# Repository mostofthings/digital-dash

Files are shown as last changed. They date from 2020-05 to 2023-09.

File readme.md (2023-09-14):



# Raspberry Pi Digital Dash

The goal of this project is to create a universal digital gauge readout for racecar applications. The core aims of this project are:

## To display easy to read data in an attractive format.

The final product should, as much as possible, look as good or better than a bank of physical gauges.



## To offer short-term historical data readout.

When driving a racecar under duress, it's often impossible to look at 7-plus-gauges and make sure that everything seems in spec. The ultimate goal of this project is to add a chart of recent historical data - think like a CPU monitor - of relevant data over a short period of time. In the pits or on the grid, the driver can peek at the data and make sure that all the systems of the car are healthy and well, even when operating under extreme conditions.

## To provide this functionality at minimal cost

Fully outfitting a racecar dash can easily cost a couple thousand bucks. One of the goals of this project is to minimize financial input and maximize efficacy and accuracy. That, friends, is the American Dream. To this end, the physical hardware involved is as inexpensive as possible, and the sensors used will, as much as possible, be all off-the-shelf, readily-available, universally-fittable ones from your favorite Large Corporate Autoparts Store.

On the computer hardware side, this project utilizes an Arduino Uno, a Raspberry Pi, and corresponding Pi 7" touch screen. I will be making use of a 3D printer, and wherever possible will be providing .stl files of any custom parts made. 

## To calibrate those sensors as accurately as possible

It's one thing for it to be cheap, and another for it to be cheap AND good. Most automotive sensors operate by providing various levels of resistance under different circumstance, and using the Arduino, we use that resistance to monitor a reference voltage. Most sensors - cheap or expensive, are assumed to have a linear response. Early testing for this project indicates that that's not always the case. 

While Mostly linear, a more curvilinear response is often seen. While this may not seem like that big of a deal, that's wholly dependent on where those curves are. In testing for the water temp sensor, the response of the sensor changes almost exponentially at the top end of its operating range - exactly where we need it the most. Various strategies will be employed to make sure that the readings on the gauge are the actual conditions going on in the car. 

## To allow this project to be replicated by others

If you too have around $250, know your way around a Raspberry Pi functionally well, and possess a willingness to walk into an Autozone, you too can replicate this exact setup. I have in MY mind specific goals for functionality, but I'm sure others may want different results to match with their particular corner of the vehicular world. Other projects similar to this one already exist, but hopefully by providing expanded functionality and ample information, this too can gain a bit of traction. Ultimately, I'll be happy to have the results of this project for myself, but I'd love it if anyone else out there found some utility out of it as well.

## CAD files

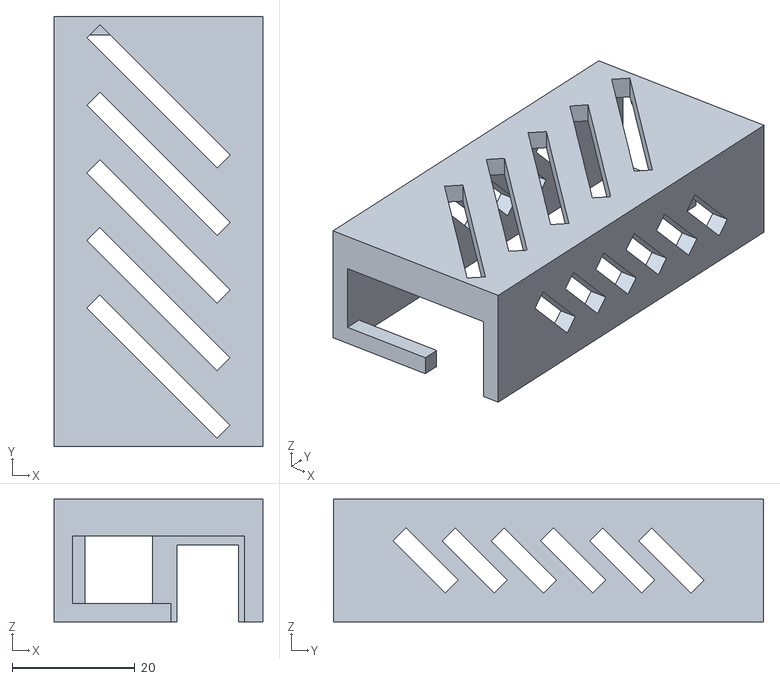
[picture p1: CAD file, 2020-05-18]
3d-print-stl-files/buck-converter-case-top.stl
34.0 x 70.0 x 20.0

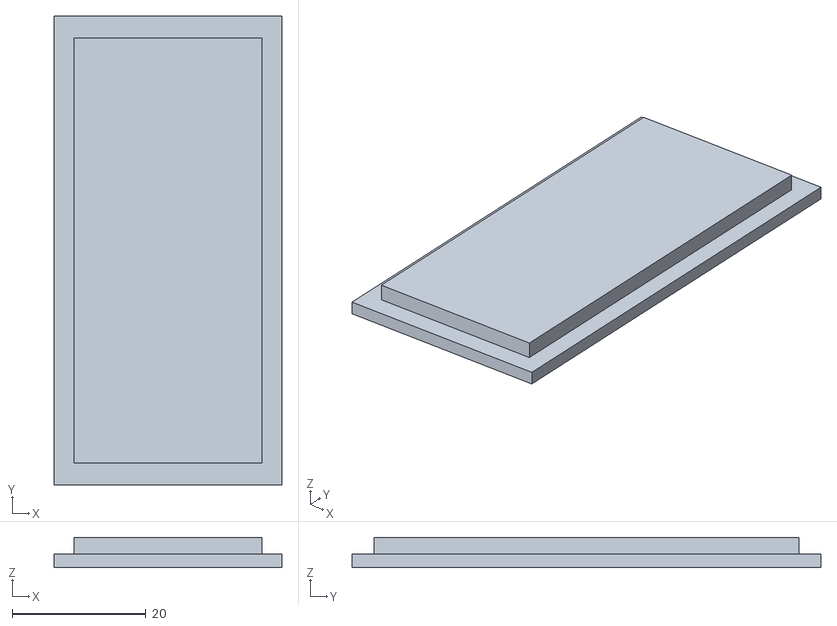
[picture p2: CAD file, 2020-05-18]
3d-print-stl-files/buck-converter-case-bottom.stl
34.0 x 70.0 x 4.50

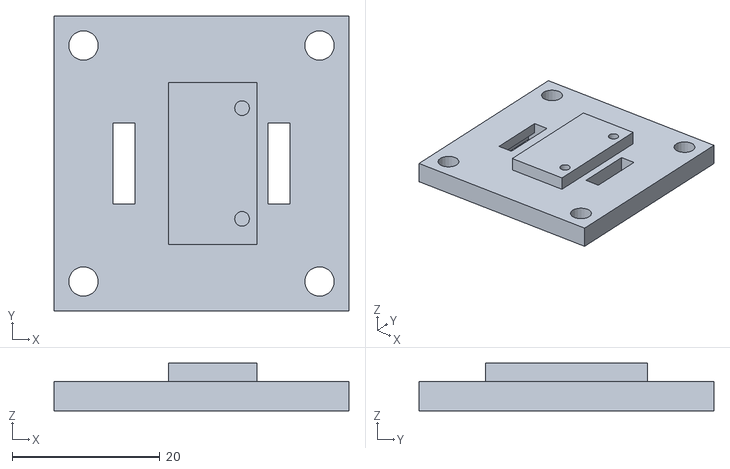
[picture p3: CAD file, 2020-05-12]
3d-print-stl-files/MMA8451 static car mount base.stl
40.0 x 40.0 x 6.50

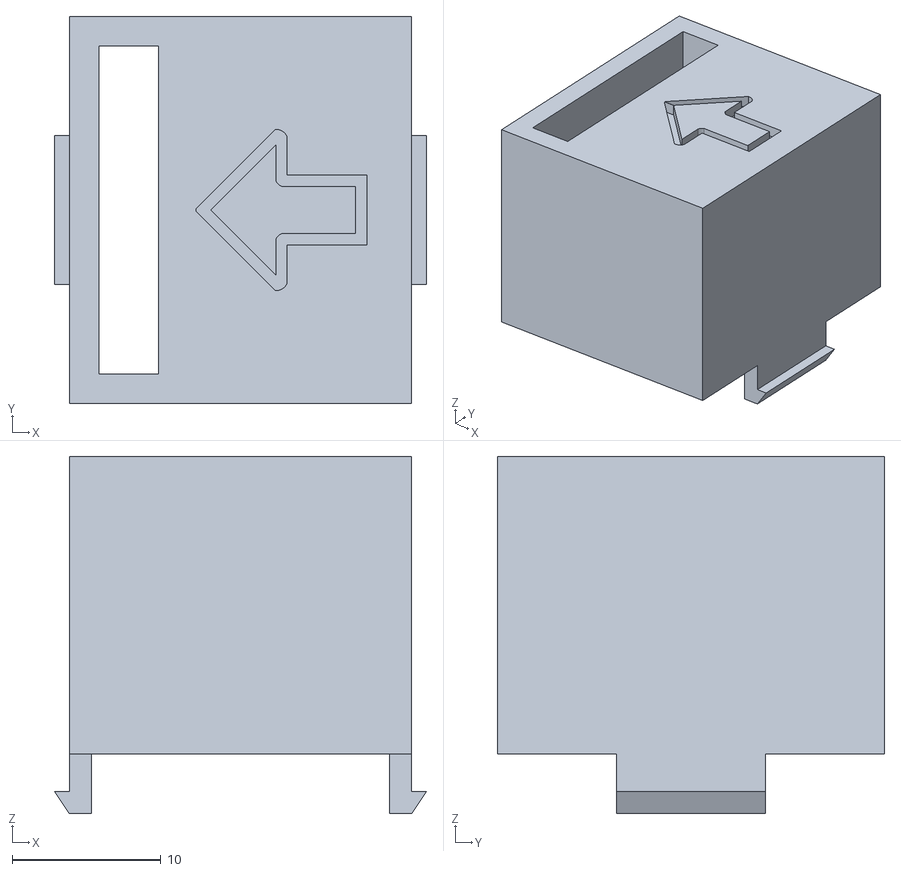
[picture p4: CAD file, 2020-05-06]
3d-print-stl-files/MMA8451 static car mount top.stl
25.0 x 26.0 x 24.0

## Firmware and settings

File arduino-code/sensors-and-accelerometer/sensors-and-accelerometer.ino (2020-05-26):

#include <math.h>
#include <Wire.h>
#include <Adafruit_MMA8451.h>
#include <Adafruit_Sensor.h>
#include <Adafruit_NeoPixel.h>
#ifdef __AVR__
#include <avr/power.h> // Required for 16 MHz Adafruit Trinket
#endif

#define PIXEL_PIN    6  // Digital IO pin connected to the NeoPixels.
#define PIXEL_COUNT 16  // Number of NeoPixels

Adafruit_NeoPixel strip(PIXEL_COUNT, PIXEL_PIN, NEO_GRB + NEO_KHZ800);

Adafruit_MMA8451 mma = Adafruit_MMA8451();

char receivedChar;
String receivedMessage;

int rawValue;
unsigned long duration;
float periodInSeconds;
float unroundedRPM;
int roundedRPM;
int rpmToSend;
int lastKnownGoodRPM;
int blinkCounter = 0;
unsigned long timeNow;
bool isDemo = false;
unsigned long demoStart;
int demoDelay = 2000;

bool masterWarn = false;
String warning = "warn";

const byte DATA_MAX_SIZE = 32;
char data[DATA_MAX_SIZE];

String waterTemp;
String boostPressure;
String fuelPressure;
String airFuelRatio;
String oilPressure;
String oilTemp;
String rpm;

String xAccel;
String yAccel;
String zAccel;

void setup(void) {
  Serial.begin(9600);
  strip.begin(); // Initialize NeoPixel strip object (REQUIRED)
  strip.setBrightness(255);
  strip.show();  // Initialize all pixels to 'off'
  pinMode(7, INPUT);

  if (! mma.begin()) {
    Serial.println("Accelerometer not found");
  }

  mma.setRange(MMA8451_RANGE_4_G);

  pixelsDemo();
}



void loop() {
  timeNow = millis();

  /* Get a new sensor event */
  sensors_event_t event;
  mma.getEvent(&event);

  rawValue = analogRead(A0);
  waterTemp = (String) "WT" + rawValue;
  rawValue = analogRead(A1);
  boostPressure = (String) "BP" + rawValue;
  rawValue = analogRead(A2);
  oilPressure = (String) "OP" + rawValue;
  rawValue = analogRead(A3);
  airFuelRatio = (String) "WB" + rawValue;
  rawValue = analogRead(A4);
  oilTemp = (String) "OT" + rawValue;


  duration = pulseIn(7, HIGH, 100000); // set for min of 500 RPM
  //  rpm = (String) "ER" + duration;
  if (duration > 0) {
    rpmToSend = calculateRPM(duration);
  } else {
    rpmToSend = 0;
    lastKnownGoodRPM = 6000;
  }
  rpm = (String) "ER" + rpmToSend;

  rawValue = event.acceleration.x * 100;
  xAccel = (String) "XA" + rawValue;
  rawValue = event.acceleration.y * 100;
  yAccel = (String) "YA" + rawValue;
  rawValue = event.acceleration.z * 100;
  zAccel = (String) "ZA" + rawValue;

  if (!isDemo) {
    strip.clear();
    for (int i = 0; i < PIXEL_COUNT; i ++) {
      int rpmCounter = i * 250 + 3250;
      if (rpmToSend >= rpmCounter) {
        if (rpmCounter <= 4000) {
          strip.setPixelColor(i, strip.Color(0, 255, 0));
        } else if ( rpmCounter <= 5000) {
          strip.setPixelColor(i, strip.Color(255, 255, 0));
        } else if ( rpmCounter <= 6000) {
          strip.setPixelColor(i, strip.Color(255, 0, 0));
        } else if ( rpmCounter <= 7000) {
          strip.setPixelColor(i, strip.Color(0, 0, 255));
        }
      }
    }
  }

  if ( rpmToSend >= 7150) {
    blinkLeds(255);
  } else if (!masterWarn) {
    blinkCounter = 0;
  }

  while (Serial.available() > 0) {
    delay(2);
    static char endMarker = '\n';
    receivedChar = Serial.read();
    

    if (receivedChar == endMarker) {

      return;
    } else {
      receivedMessage += receivedChar;
    }
  }

  if (receivedMessage == warning) {
    masterWarn = true;
//    Serial.println("EM" + receivedMessage + ",");
    receivedMessage = '\0';
  }
  
  if (receivedMessage != '\0') {
    strip.setBrightness(receivedMessage.toInt());
    demoDelay = 750;
    pixelsDemo();
//    Serial.println("EM" + receivedMessage + ",");
    receivedMessage = '\0';
  }


    if (masterWarn){
      blinkLeds(16711680);
    }

  strip.show();

  while (millis() < timeNow + 100) {
    //total delay of 100ms
  }

  if (isDemo && millis() > demoStart + demoDelay) {
    isDemo = false;
  }



  /* Display the results (acceleration is measured in m/s^2) */
  Serial.println(waterTemp + "," + boostPressure + "," + oilPressure + "," + oilTemp + "," +
                 airFuelRatio + "," + rpm + "," + xAccel + "," + yAccel + "," + zAccel);
}

int calculateRPM(unsigned long value) {
  periodInSeconds = value * 3.5 / 1000000;
  unroundedRPM = 60 / periodInSeconds;
  roundedRPM = round(unroundedRPM);
  if (roundedRPM <= lastKnownGoodRPM * 3) {
    lastKnownGoodRPM = roundedRPM;
  } else if (roundedRPM > lastKnownGoodRPM * 3) {
    roundedRPM = lastKnownGoodRPM;
  }
  return roundedRPM;
}

void pixelsDemo() {
  for (int n = 0; n < 16; n++) {
    if (n < 4) {
      strip.setPixelColor(n, strip.Color(0, 255, 0));
    } else if (n < 8) {
      strip.setPixelColor(n, strip.Color(255, 255, 0));
    } else if (n < 12) {
      strip.setPixelColor(n, strip.Color(255, 0, 0));
    } else if (n < 16) {
      strip.setPixelColor(n, strip.Color(0, 0, 255));
    }
  }
  isDemo = true;
  demoStart = millis();
}

void blinkLeds(unsigned long color) {
  strip.fill(color, 0);
  blinkCounter++;
  if (blinkCounter > 2) {
    strip.clear();
  }
  if (blinkCounter == 4) {
    blinkCounter = 0;
  }
}

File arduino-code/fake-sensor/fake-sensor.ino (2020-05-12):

int rawValue;
int fakeWaterTemp;
int fakeOilPressure;
int fakeFuelPressure;
int fakeBoost;
int fakeRPM;
int fakeAFR;
int fakeGForceX;
int fakeGForceY;
int counter;
String accelX;
String accelY;
String waterTemp;
String boostPressure;
String fuelPressure;
String airFuelRatio;
String oilPressure;
String rpm;
bool up = true;

void setup() {
  Serial.begin(9600);
  counter = 0;
  fakeWaterTemp = 322;
  fakeOilPressure = 409;
  fakeFuelPressure = 35;
  fakeBoost = 101;
  fakeGForceX = 10;
  fakeGForceY = 30;
  fakeAFR = 235;
  fakeRPM = 1200;
}

void loop() {
  if (up){
    fakeWaterTemp = fakeWaterTemp + 3;
    fakeOilPressure = fakeOilPressure + 3;
    fakeFuelPressure = fakeFuelPressure + 1;
    fakeBoost = fakeBoost + 3;
    fakeAFR = fakeAFR + 5;
    fakeRPM = fakeRPM + 120;
    fakeGForceX = fakeGForceX - 8;
    fakeGForceY = fakeGForceY - 8;
    if (counter >= 20){
      up = false;
      counter--;
    }
    else{
    counter++;
    }
  } else {
    fakeWaterTemp = fakeWaterTemp - 3;
    fakeOilPressure = fakeOilPressure - 3;
    fakeFuelPressure = fakeFuelPressure - 1;
    fakeBoost = fakeBoost - 3;
    fakeAFR = fakeAFR -5;
    fakeRPM = fakeRPM - 120;
    fakeGForceX = fakeGForceX + 8;
    fakeGForceY = fakeGForceY + 8;
    if (counter <= 0){
      up = true;
      counter++;
    }
    else{
    counter--;
    }
  }
  
  waterTemp = (String)"WT" + fakeWaterTemp;
  oilPressure = (String)"OP" + fakeOilPressure;
  fuelPressure = (String)"FP" + fakeFuelPressure;
  airFuelRatio = (String)"WB" + fakeAFR;
  boostPressure = (String)"BP" + fakeBoost;
  rpm = (String)"ER" + fakeRPM;
  accelX = (String)"XA" + fakeGForceX;
  accelY = (String)"YA" + fakeGForceY;
  
  Serial.println(waterTemp + "," + oilPressure + "," + airFuelRatio + "," + fuelPressure + "," + boostPressure + "," + rpm + "," + accelX + "," + accelY);
  delay(100);
}

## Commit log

2020-05-05 modified background
    [MMA8451 static car mount (1).stl, MMA8451 static car mount.stl]
2020-05-05 modified fake sensor
2020-05-06 updated 3d print files
    [MMA8451 static car mount (1).stl, MMA8451 static car mount (3).stl, MMA8451 static car mount.stl]
2020-05-07 fixed temp sensor
2020-05-12 fixed g meter
    [MMA8451 static car mount base.stl, MMA8451 static car mount top.stl]
2020-05-12 changed file structure, added gmeter reset
    [index.js]
2020-05-12 updated for AEM sensors
2020-05-14 first attempt at full sensor functionality
2020-05-17 fixed math for 0 rpm
    [index.js, sensors-and-accelerometer.ino]
2020-05-17 hnged error correction logic
    [index.js]
2020-05-18 case for converter
    [buck-converter-case-bottom.stl]
2020-05-18 added correction for rpm signal
    [buck-converter-case-top.stl]
2020-05-18 updated chart settings and fixed rpm smoothing
    [index.js]
2020-05-19 fixed logic for RPM on restart
    [index.js]
2020-05-21 moved RPM calculation logic to arduino
2020-05-26 added master warn and LED brightness control
